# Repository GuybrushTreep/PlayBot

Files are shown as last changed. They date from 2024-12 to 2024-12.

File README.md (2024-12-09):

# 🤖 PlayBot

PlayBot is an unofficial, experimental accessory for Panic Inc.'s Playdate handheld console, which transforms your console into a lovely little desktop robot. 
With its integrated charging capabilities, it can serve as a charging dock for your Playdate.

Here is a little video of Playbot (click to watch)

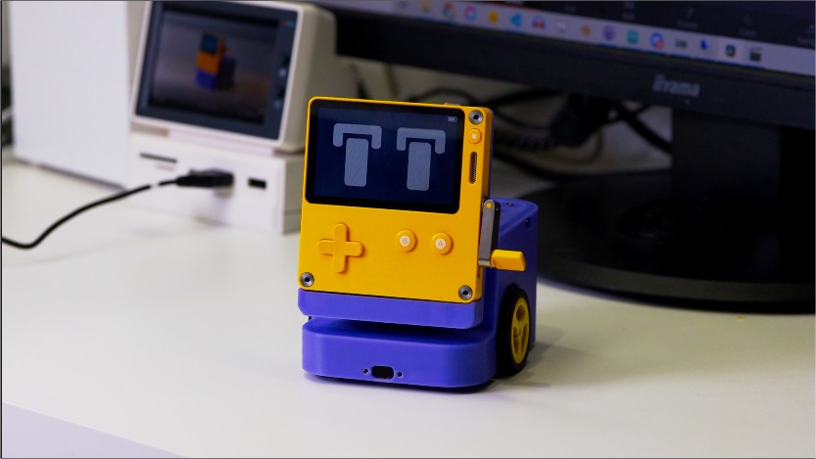
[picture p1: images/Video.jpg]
Playbot_Trailer (https://youtu.be/pZ3aDawW1vo?si=pN9pur77LKVZNdHx)


⚡ Battery life: ~45 min of autonomous operation per charge.

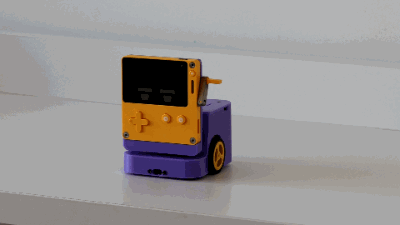
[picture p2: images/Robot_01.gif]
PlaybotAction
 PlaybotAction
PlaybotAction PlaybotAction

## ⚠️ Disclaimer

This project is not affiliated with nor endorsed by [Panic](https://panic.com/).

I cannot be held responsible for any damage, data loss, short circuit, burned down house, etc. 😘

## 🔧 Hardware

The project is based on a Teensy 4.1 microcontroller that acts as a USB hub for the Playdate and communicates over serial. 

The Playdate acts as the robot's brain and sends commands to the Teensy to control motors and gather various sensor values:

- 2 TOF distance sensors
- TEMT6000 Ambient light sensor
- 2 IR sensors
- Dual motors with encoders
- MAX1704X fuel gauge 

I'm also using the Playdate's integrated sensors:
- Accelerometer
- Microphone

Additionnal Vision AI camera powered by [Huskylens](https://www.dfrobot.com/product-1922.html) will be compatible.

PlayBot's frame is fully 3D printed. A complete bill of materials and assembly instructions can be found [here](https://github.com/GuybrushTreep/PlayBot/tree/main/hardware) 

## 💾 Firmware

You can flash the [firmware](https://github.com/GuybrushTreep/PlayBot/tree/main/src/PlayBot) using the Arduino IDE and Teensyduino add-on available [here](https://www.pjrc.com/teensy/teensyduino.html).

## 📚 Dependencies 
  - [USBHost_t36](https://github.com/PaulStoffregen/USBHost_t36) by [PaulStoffregen](https://github.com/PaulStoffregen)
  - [Encoder](https://github.com/PaulStoffregen/Encoder) by [PaulStoffregen](https://github.com/PaulStoffregen) 
  - [drv8835-motor-shield](https://github.com/pololu/drv8835-motor-shield) by [pololu](https://github.com/pololu)
  - [SD library](https://github.com/arduino-libraries/SD) by [Arduino](https://github.com/arduino-libraries)
  - [Servo library](https://github.com/arduino-libraries/Servo) by [Arduino](https://github.com/)
  - [MAX1704X](https://github.com/adafruit/Adafruit_MAX1704X) by [adafruit](https://github.com/adafruit)
  - [PID_V1](https://github.com/br3ttb/Arduino-PID-Library) by [br3ttb](https://github.com/br3ttb)
  - [WS2812FX](https://github.com/kitesurfer1404/WS2812FX) by [kitesurfer1404](https://github.com/kitesurfer1404/WS2812FX)
  - [CircularBuffer](https://github.com/rlogiacco/CircularBuffer) by [rlogiacco](https://github.com/kitesurfer1404/WS2812FX)

## 📱 Companion App

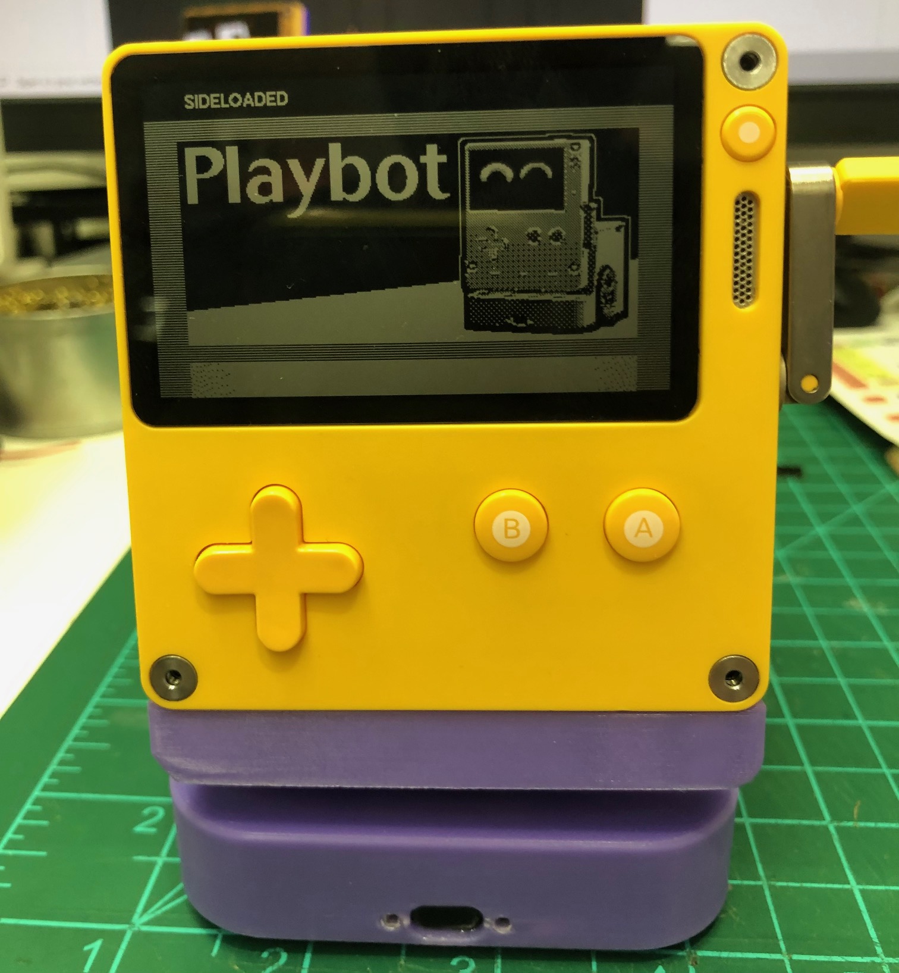
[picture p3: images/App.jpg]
Power Board


The app, written in Lua, needs to be sideloaded onto the Playdate and is located in a [separate repository](https://github.com/GuybrushTreep/pd-playbot-app).

## 🎨 Custom rig
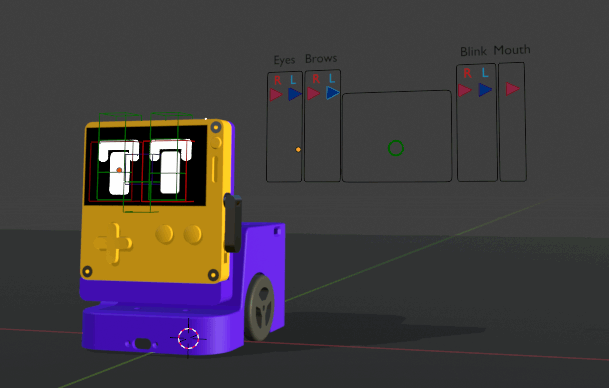
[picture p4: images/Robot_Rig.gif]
PlaybotRig


A Custom rig and sequence exporter written in python is also available for Blender in a [seperate repository](https://github.com/GuybrushTreep/Playbot_Rig).
Animate, render and export custom animation sequences!

## ⚠️ Known Issues
* ToF sensors show unreliable readings when pointing into empty space (possibly defective units) - planning to replace with IR sensors
* Battery gauge readings become erratic under high current load - investigation ongoing

## 📜 License

[MIT](https://choosealicense.com/licenses/mit/)

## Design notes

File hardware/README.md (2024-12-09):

## Summary
- [Bill of materials](#bill-of-materials)
- [Recommended tools](#Recommended-tools)
- [3d printed parts](#3d-printed-parts)
- [Custom PCBs](#custom-pcbs)
    - [Power board](#power-board)
    - [Main board](#main-board)
- [Assembly](#assembly)
    - [Top Frame](#Top-Frame)
        - [Servo mod](#servo-modification)
        - [Brass insert](#brass-inserts)
    - [Middle Frame](#middle-frame)
        - [DRV8835](#drv8835)
        - [Power harness](#power-harness)
    - [Lower Frame](#lower-frame)
        - [Ball caster wheels](#ball-caster-wheels)
        - [ITR20001-sensors](#itr20001-sensors)
    - [console base](#console-base)
        - [Usb](#usb)  
    - [Shell](#Shell)
        - [light sensor](#TEMT6000-light-sensor)
        - [switch](#SPDT-switch)
        - [TOF10120](#TOF-sensors)
     - [Putting Everything Together](#Putting-Everything-Together)
# Bill of materials

This folder contains all the files and instructions to build Playbot.

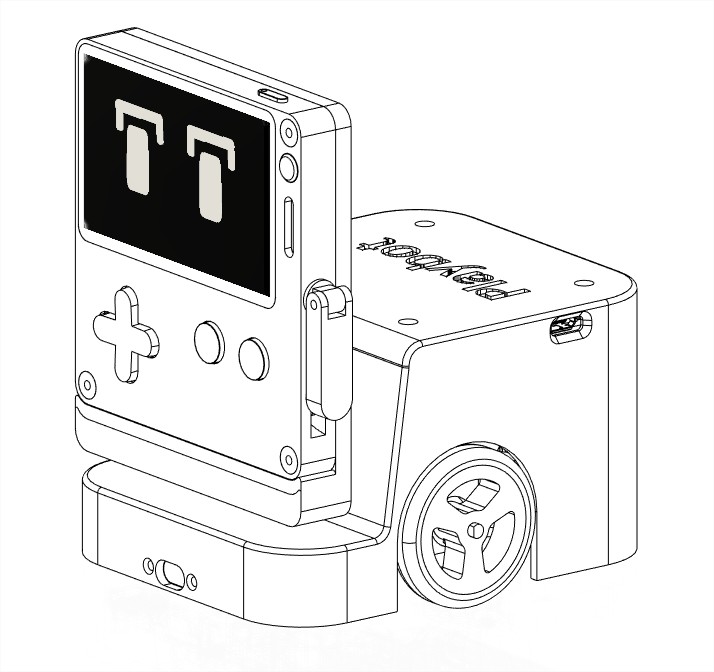
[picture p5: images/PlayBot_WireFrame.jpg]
A drawing of the robot from Fusion


## Hardware

|Item| Quantity|Notes
|---|---|---|
|Custom PCBs|2|Order from [JLCPCB](https://jlcpcb.com) see Gerber files and BOMs
|Teensy 4.1 microcontroller| 1|[PJCRC store](https://www.pjrc.com/store/teensy41.html)
| TOF10120| 2| [AlliExpress](https://fr.aliexpress.com/item/1005006355757514.html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,scm-url:1007.40050.354490.0,pvid:43a39a83-8bf7-4a9d-b2aa-4d4200da0014,tpp_buckets:668%232846%238107%231934&isseo=y&pdp_npi=4%40dis%21EUR%214.29%214.29%21%21%214.68%214.68%21%402103895417271255595797778e7ce3%2112000037973716121%21rec%21FR%21%21ABXZ&utparam-url=scene%3ApcDetailTopMoreOtherSeller%7Cquery_from%3A)
| Low profile headers 12 pins| 1| [Example  AlliExpress](https://fr.aliexpress.com/item/1005006252502654.html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)
| SG90 servo | 1 | [Example AlliExpress](https://fr.aliexpress.com/item/1005006522732429.html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)
| ITR20001 | 2| [Example AlliExpress](https://fr.aliexpress.com/item/1005007697148589.html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)
TEMT6000 ambient light sensor | 1 | [Example AlliExpress](https://fr.aliexpress.com/item/33034437035.html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)
| mini ball caster wheels| 2| [Example AlliExpress](https://fr.aliexpress.com/item/1005007392098564.html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,scm-url:1007.40050.354490.0,pvid:af027fb5-cab6-4c62-8038-6874711e65c5,tpp_buckets:668%232846%238112%231997&isseo=y&pdp_npi=4%40dis%21EUR%210.21%210.21%21%21%210.23%210.23%21%402103895417271259822313224e7ce3%2112000040559594027%21rec%21FR%21%21ABXZ&utparam-url=scene%3ApcDetailTopMoreOtherSeller%7Cquery_from%3A)
| N20 6V 500RPM motors| 2| [Example AlliExpress](https://fr.aliexpress.com/item/1005004999529855.html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)
| N20 wheels| 2| [Example AlliExpress](https://fr.aliexpress.com/item/1005006640418754.html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)
| DRV8835 Dual Motor Driver Carrier| 1| [Pololu](https://www.pololu.com/product/2135)
| M2 Screws| 1 box| [Example AlliExpress](https://fr.aliexpress.com/item/1005002426046826.html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)
| M2 and M3 nylon nut set| | [Example Alliexpress](https://fr.aliexpress.com/item/33017191364.html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)
| M2 X 5 insert| 1 box| [Example AlliExpress](https://fr.aliexpress.com/item/1005007481465353.html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)
| USBC connectors Male/Female| 1 | [Example AlliExpress](https://fr.aliexpress.com/item/1005004807492800.html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)
| SPDT switch| 1 | [Example AlliExpress](https://fr.aliexpress.com/item/32812689209.html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)
| Battery Lipo 1S 15000mAh 504050 | 1 | [Example AlliExpress](https://fr.aliexpress.com/item/32988366494.html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)
| Pre crimped JST SH connector set 3 to 7 pins (pre crimped is much easier)| 1 | [Example AlliExpress](https://fr.aliexpress.com/item/1005004705798387.html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)
| JST PH connector Male/Female 2/4 pins | 1 box | [Example AlliExpress](https://fr.aliexpress.com/item/1005006498660940.html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)
| Flanged ball bearing 6X3X2.5 | 2 | [Example AlliExpress](https://fr.aliexpress.com/item/32969015516.html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)
| Nylon M3 X 40 screw  | 1 | [Example AlliExpress](https://fr.aliexpress.com/item/1005003130662735.html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)
| Magnets 6X3| 4 | [Example AlliExpress](https://fr.aliexpress.com/item/1005006291065081.html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)
| Servo pull rod 120 mm| 1 | [Example AlliExpress](https://www.aliexpress.us/item/3256807116664206.html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)
| 1.3mm push rod connector| 1 |[Example AlliExpress](https://www.aliexpress.us/item/2255800230609318.html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)
| Micro SD card| 1 |
| 24 AWG wire in various colors| 1 |
| HuskyLens (optional, for advanced AI vision) | 1 | [DFRobot](https://www.dfrobot.com/product-1922.html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)
|A playdate !| 1 | [Play.date](https://play.date/)

**Price range**: Around 100/120 $ (without shipping) **per bot**. Custom PCBs are cheap (10$ a piece) but you have to order in bulk of 5. 

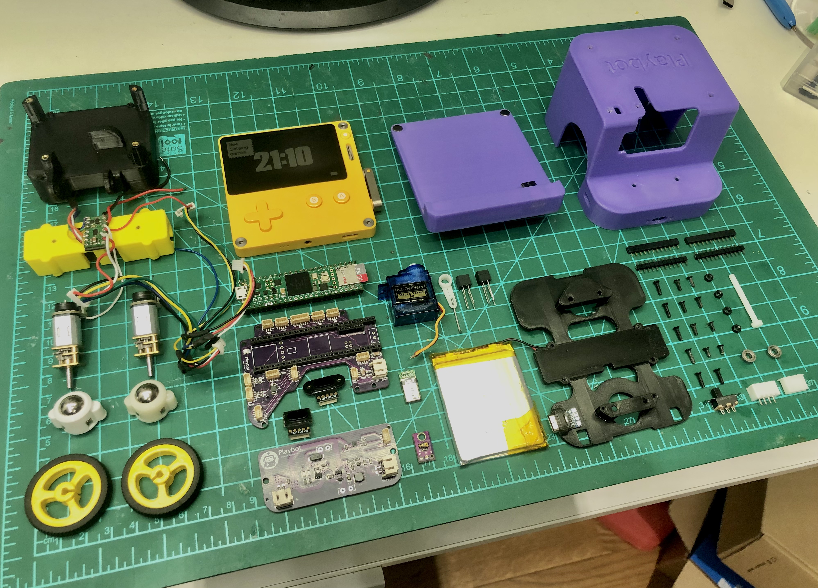
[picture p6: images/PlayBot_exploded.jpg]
Parts


⚠️⚠️ Playbot is not a plug-and-play project as it requires a lot of soldering and custom connectors/wires. ⚠️⚠️

**This is a first prototype, and I'm already working on a V2 with only one PCB and less soldering involved.**

## Recommended tools

| Tool | Notes |
|---|---|
| Soldering Iron |  |
| Flux | For clean solder joints |
| Heat Shrink Tubing | 1/2 mm|
| Precision Screwdrivers |  |
| JST PH Crimp Tool | For JST PH connectors |
| JST SH Crimp Tool | Optional - expensive, can use pre-crimped wires instead |
| Kapton Tape |  |
|  Wire strippers  | (20-30 AWG) |
|  Tweezers  ||
|  Helping hands with magnifying glass|  |

## 3D Printed Parts

STL files are available [here](../hardware/3dPrinted_Parts)

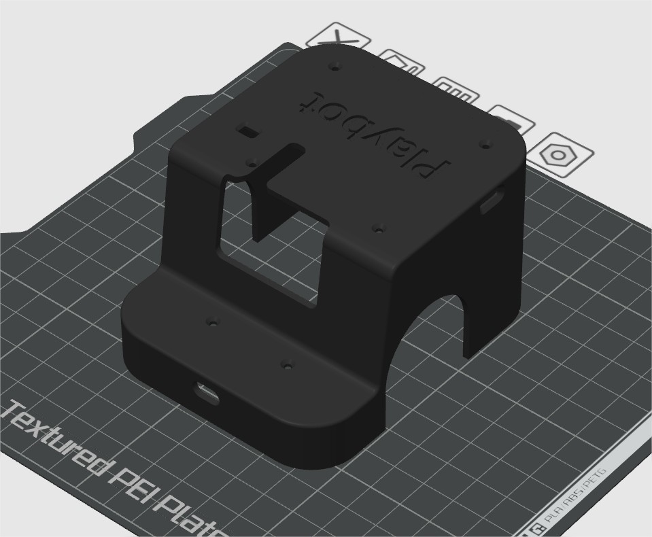
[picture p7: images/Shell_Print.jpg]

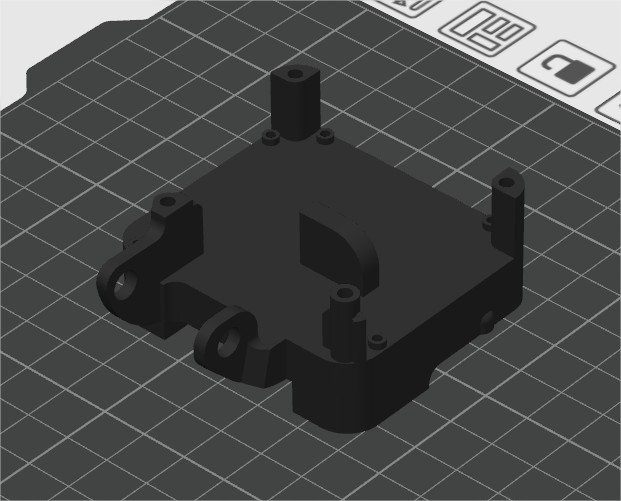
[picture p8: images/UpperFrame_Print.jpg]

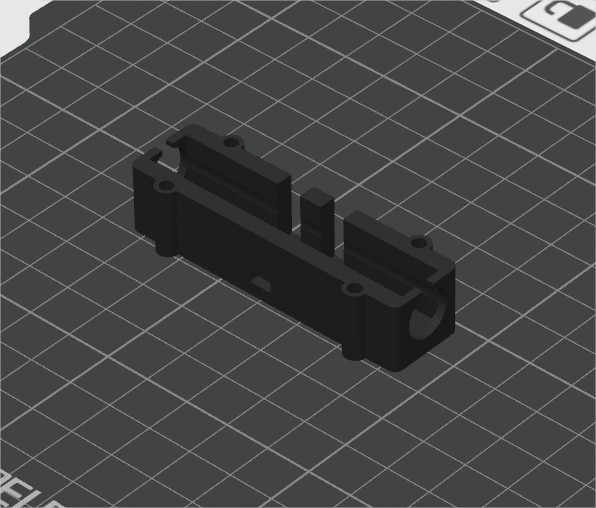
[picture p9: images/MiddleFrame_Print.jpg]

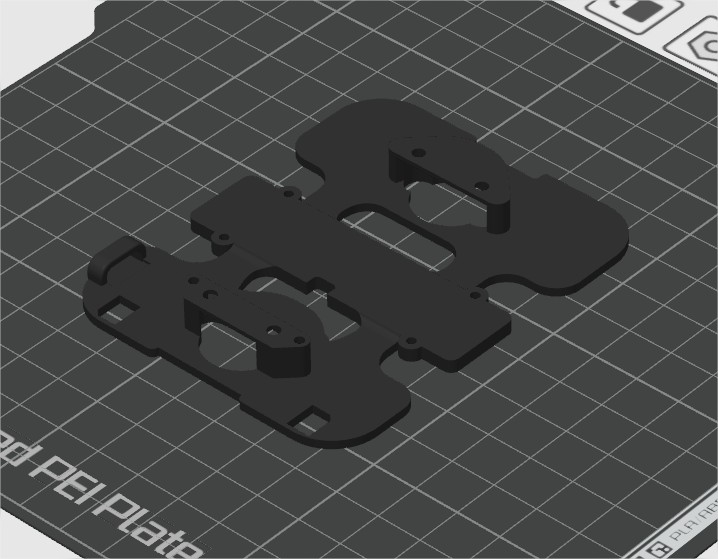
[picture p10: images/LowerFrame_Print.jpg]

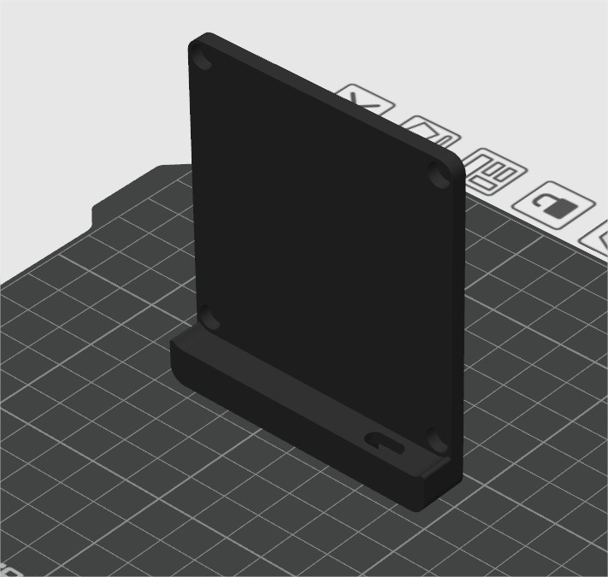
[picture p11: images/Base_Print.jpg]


I print these on a Bambu Lab A1 mini with generic PLA. 

## Custom PCBs
### Power Board
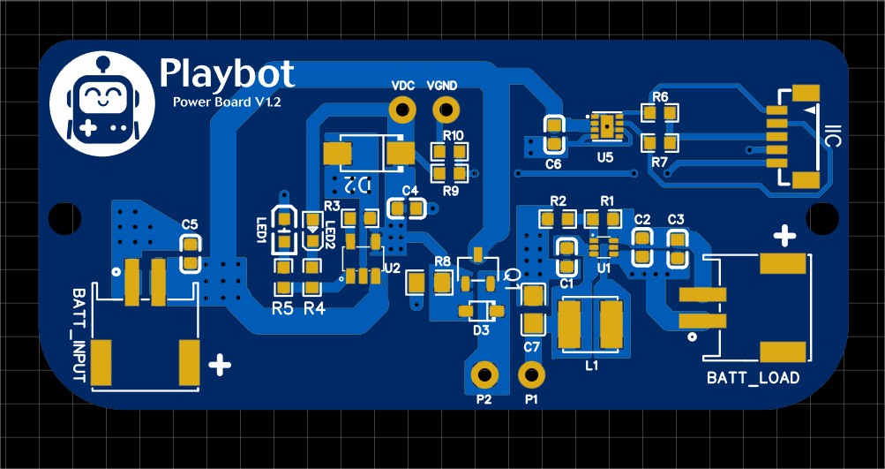
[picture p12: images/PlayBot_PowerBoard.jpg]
Power Board

1-cell LiPo charger (MCP73831) with 5V boost converter (TPS61023) and fuel gauge (MAX17048). The board is capable of load-sharing and can be plugged in while running the robot. 
This board will also charge the Playdate when the robot is active. 
Red LED when charging/Yellow LED when fully charged.

### Main Board 

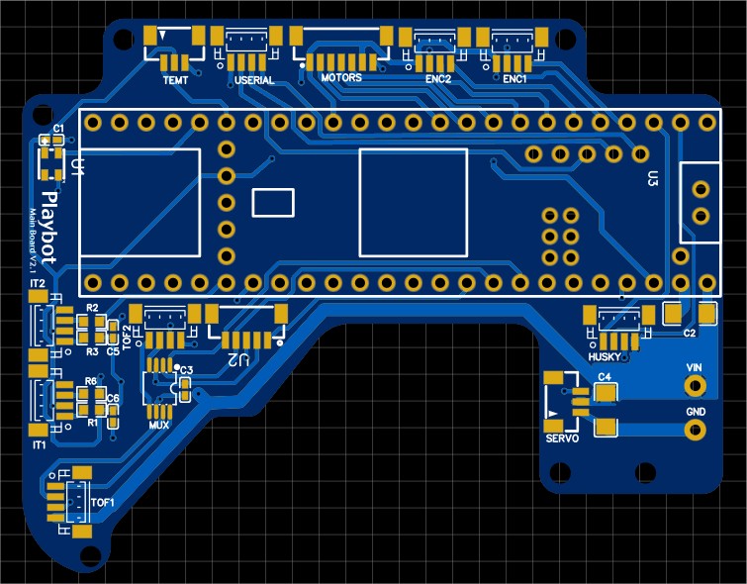
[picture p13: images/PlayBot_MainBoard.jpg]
Main board


A board that connects various sensors/motors/servos and distributes power to the Teensy.
You will need special low-profile headers to fit the Teensy inside the case.
 
 ⚠️⚠️ **Important: To protect your battery-powered Teensy, it is recommended to cut the USB power trace.** ⚠️⚠️

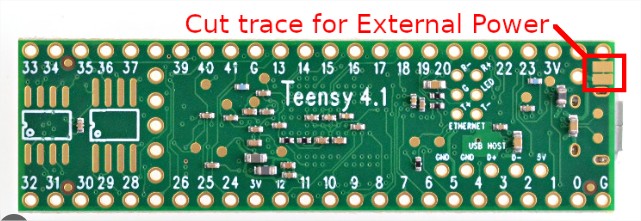
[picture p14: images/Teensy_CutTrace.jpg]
 

- Solder male headers on Teensy main side pins and USB host pins.

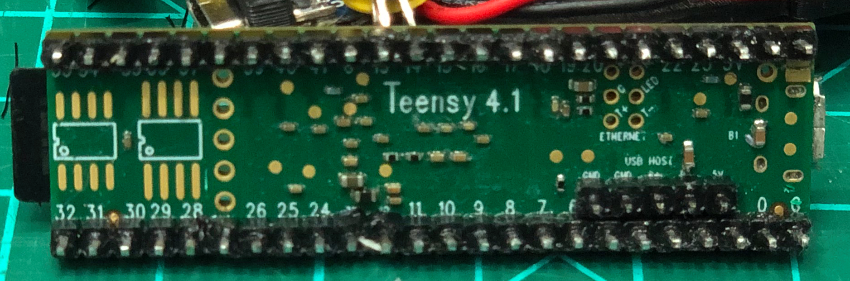
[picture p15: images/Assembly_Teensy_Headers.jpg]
 

- Solder female low-profile headers on the Playbot main board. 

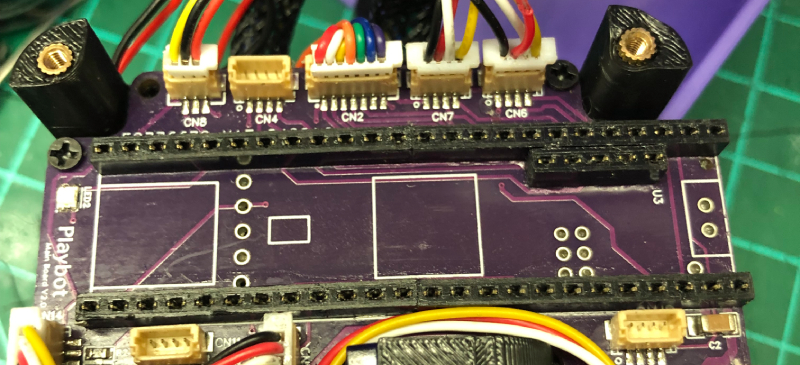
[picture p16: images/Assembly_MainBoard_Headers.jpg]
Main board
 

## Assembly

### Testing

⚠️⚠️ For every step, I strongly advise you to double-check your connections, flash the test [firmware](https://github.com/GuybrushTreep/PlayBot/tree/main/src/Playbot_SensorsTest) to the Teensy, plug in your components, and test the boot sequence to ensure everything is working correctly. ⚠️⚠️ 

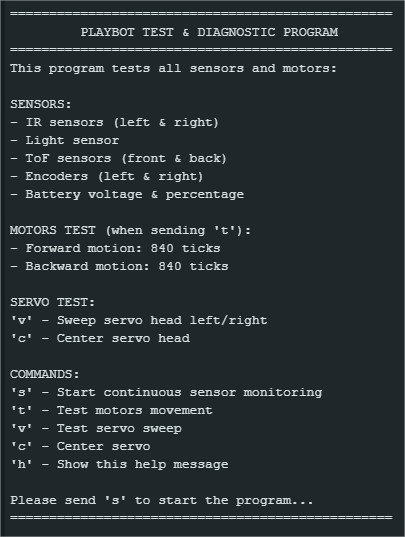
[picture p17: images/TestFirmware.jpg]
Test


### Top Frame

Main board

#### Servo Modification:

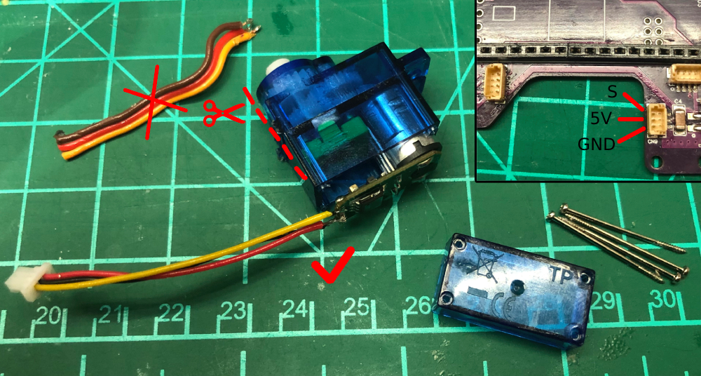
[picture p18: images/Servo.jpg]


- Cut the left plastic ear flush.
- Open the servo case by removing the 4 screws.
- Cut/desolder the wires. Take note of the color code: **brown** -> **GND** | **red** -> **V+** | **orange** -> **signal**.
- Solder new wires with a JST SH connector. Pay attention to the **servo** connector wiring. 

Also, due to tight space constraints, the servo horn needs to be modified.

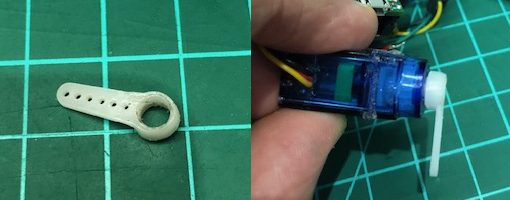
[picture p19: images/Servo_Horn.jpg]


The hole is enlarged with a soldering iron and press-fitted onto the servo axle while soft, center the servo position with the test firmware before screwing it.

#### Brass Inserts

Check this excellent [tutorial](https://www.youtube.com/watch?v=KC1LLU54DKU&ab_channel=GeekDetour) for heated brass inserts on PLA.

- Add 5 brass inserts on the top of the frame:

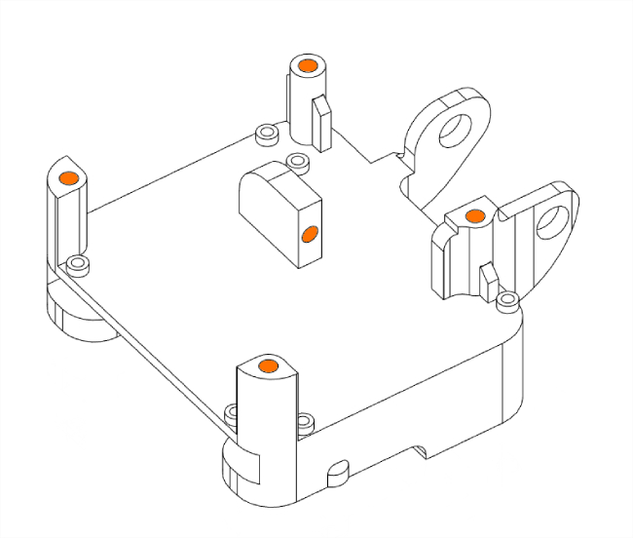
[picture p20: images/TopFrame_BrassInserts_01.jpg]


- And 4 others on the frame's bottom: 

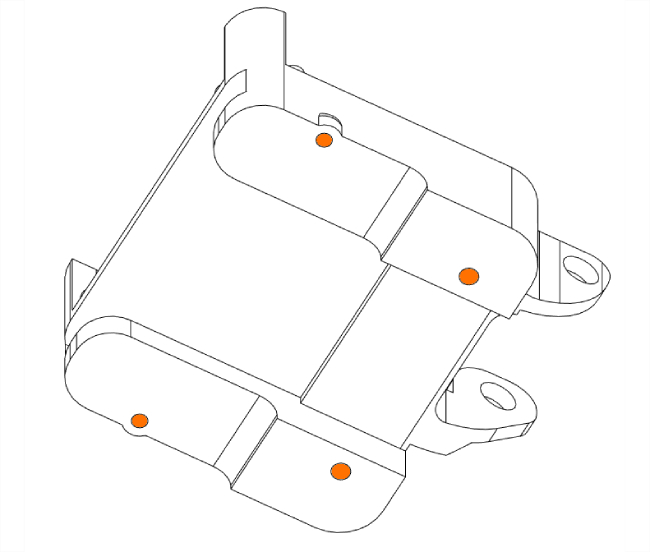
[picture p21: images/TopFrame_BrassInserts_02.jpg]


- Screw the mainboard directly into the frame using M2 * 4 screws.
- Press-fit the 2 ball bearings into the frame
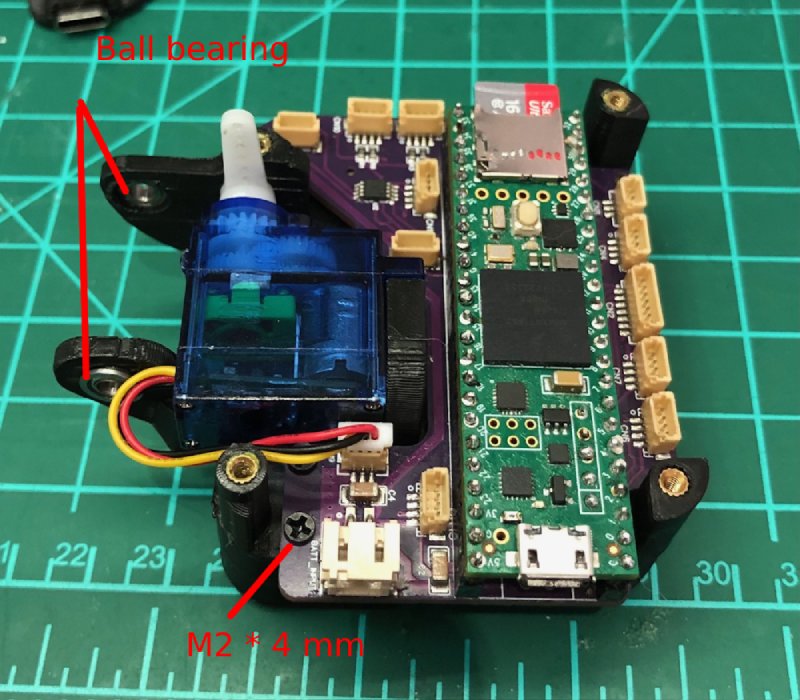
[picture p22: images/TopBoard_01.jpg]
Main board


- Solder the power switch and USB-C input to the power management board. Press-fit the USB-C plug into the bottom frame. You can add a bit of hot glue to secure it to the frame.
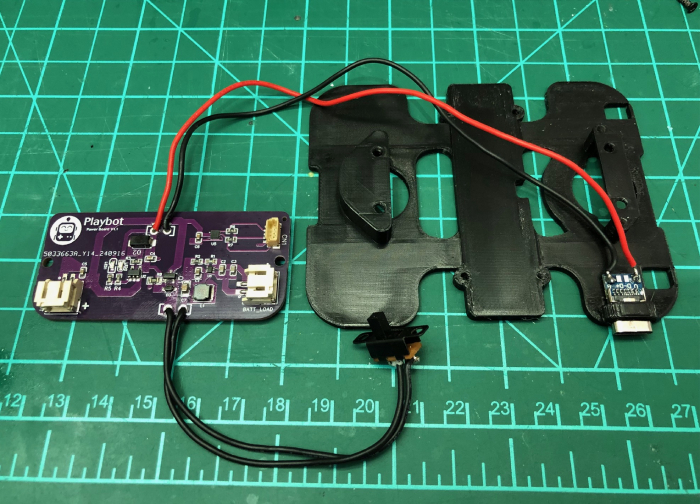
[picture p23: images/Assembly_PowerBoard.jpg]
Main board


- You can now screw the power board to the frame's bottom. 
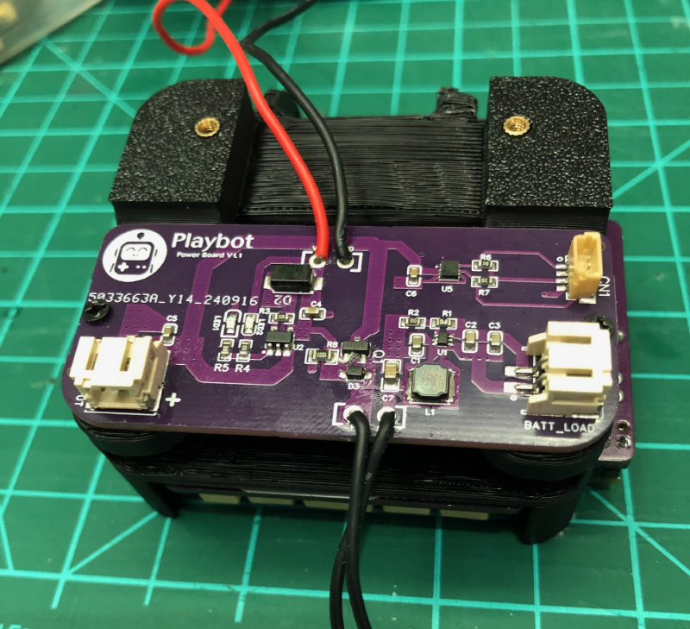
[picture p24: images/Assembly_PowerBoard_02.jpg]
Main board


- The lipo baterry slides into a dedicated socket on the frame.
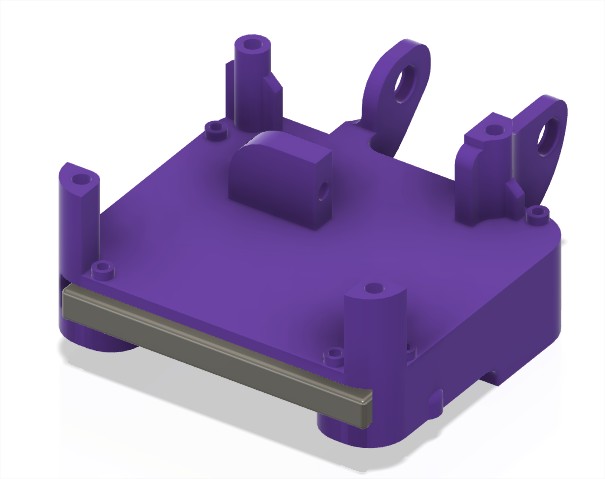
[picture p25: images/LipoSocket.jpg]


### Middle Frame
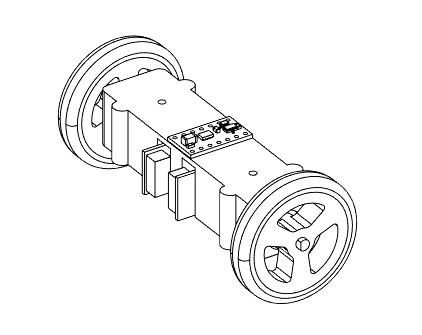
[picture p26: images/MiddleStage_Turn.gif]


- Add 4 brass inserts.

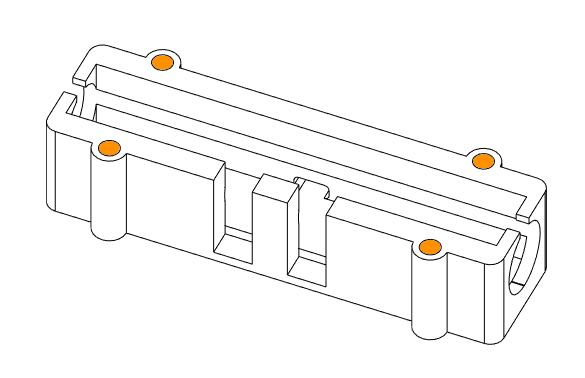
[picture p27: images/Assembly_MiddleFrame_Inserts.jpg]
Middle_01


#### DRV8835
The DRV8835 board is attached directly in the middle of the part with double-sided adhesive.

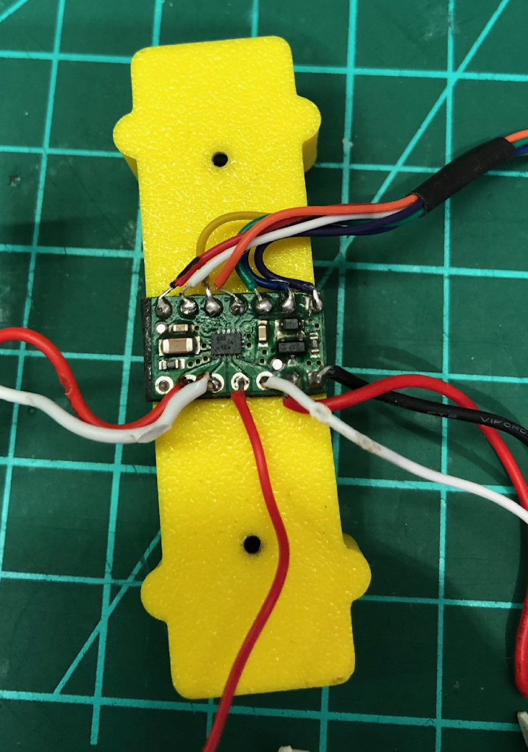
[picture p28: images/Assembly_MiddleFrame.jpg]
Middle_01


- Solder pins MODE, AIN1, AIN2, BIN1, BIN2, VCC, and GND to a 7-pin JST SH connector for the motors Connector.

Please check the [Pololu](https://www.pololu.com/product/2135) page for more information about this board.

DRV8835

- Create a custom plug for motors. Power comes from the DRV8835 board (M1 and M2), and the 4 other wires are for encoder feedback (ENC1, ENC2).

Motors
Motors

- Before adding motors, you must attach the middle and top frame together with 2 M2 screws. 

MiddleFrame

#### Power Harness

Create a power harness with JST **PH** connectors to power the main board and DRV8835 from the power board's power output. 

PowerHarness

** note: I replaced the Main board's PH connector with simple solder pads on the last revision** 

## Lower Frame
LowerStage

### Ball Caster Wheels

- Remove screws, insert the ball caster wheels, and screw them back to the frame.
BallCaster

## Console Base 

ConsoleBase

### USB 

- Create a USB plug connected to a 4-pin JST **PH** connector. 
You can add a bit of hot glue to secure the PH connector.

Base_USB

- Create a 4-pin **PH** to **SH** connector that will connect to **USERIAL** connector on the main board.

Base_Plug

Base_Plug

The USB plugs comes with little plastic rings that you can glue to the part.

- Press-fit magnets into the dock.

Magnet

## Shell
Shell

### TEMT6000 Light Sensor

- Solder a 3-pin JST **SH** connector that connects to **TEMT** connector on the main board.

TEMT

- Screw and bolt it to the shell.

TEMT02

### SPDT Switch

- Screw and bolt the switch to the shell.

Switch

### TOF Sensors

- Solder a 4-pin JST **SH** connector that connects to **TOF1** and **TOF2** on the main board. You can cut RX/TX wires as we use I²C through a 2-channel multiplexer.

TOF01

- Attach both sensors at the front and back of the shell with M2.5x6 screws and nylon nuts. 

TOF01

## Putting Everything Together

At this point, you're almost done. Congratulations! I assume you've already tested every component by flashing the test firmware. 

⚠️⚠️ Don't forget to flash the micro SD card with the [animation files](https://github.com/GuybrushTreep/Playbot_Rig/tree/main/Animations/Export). You can still access the SD card from your computer with the help of this library: https://github.com/KurtE/MTP_Teensy ⚠️⚠️

If no errors show up, you're good to assemble the remaining parts in this order:

TOF01
TOF01
TOF01
TOF01
TOF01

This is the tricky part, as everything will be tightly packed inside the shell.

Attach the screen base with M3 screw, do not overtighten it. 
Cut a Servo pull rod at 20 mm and attach it to the servo's arm with a connector.

TOF01

Congratulations, your Playbot is now complete!

TOF01

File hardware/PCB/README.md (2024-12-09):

# JLCPCB Options

Parts

Parts

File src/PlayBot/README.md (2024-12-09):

# Robot Controller - Arduino Project

Firmware for a robot using Teensy microcontroller that communicates with a Playdate device.

## Core Components

### Main Program (PlayBot.ino)
- Main program loop and initialization
- Orchestrates all subsystems
- Manages communication between components

### Managers

#### AnimationManager (AnimationManager.h)
- Handles animation playback from SD card
- Controls servo movements
- Manages motor coordination for animations
- Real-time frame processing

#### BatteryManager (BatteryManager.h)
- Battery voltage monitoring via MAX17048 gauge
- Charging state detection
- Power state reporting to Playdate

#### CommunicationManager (CommunicationManager.h)
- USB serial communication with Playdate
- Message parsing and routing
- Protocol handling for all subsystems

#### LEDController (LEDController.h)
- WS2812 LED control
- Status indication

#### MotorController (MotorController.h)
- DRV8835 motor driver control
- PID-based motor control
- Encoder feedback processing
- Rotation and movement commands

#### SensorManager (SensorManager.h)
- ToF distance sensors management
- IR edge detection
- Light sensor readings
- Collision detection
- Sensor data aggregation and reporting

#### StorageManager (StorageManager.h)
- SD card initialization
- File system management

### Support Files

#### Config.h
- System-wide configuration parameters
- Pin definitions
- Timing constants
- Sensor thresholds

#### Debug.h/cpp
- Debugging infrastructure
- Error logging
- Setup error tracking
- Log buffering and transmission

#### DistanceTracker.h
- Tracks total distance traveled
- Persistent distance logging
- Movement statistics

#### HardwareConfig.h/cpp
- Hardware-specific configurations
- Pin assignments
- Physical constants
- Hardware object initialization

## Communication Protocol

Message Protocol Details:

Outgoing (Arduino -> Playdate):
- "msg b/percent/voltage/charging"
  Example: "msg b/85.20/3.7/1" (85.20% battery, 3.7V, charging)

- "msg d/irRight/irLeft/tofFront/tofBack/encRight/encLeft/light/batteryVoltage/charging/distanceM"
  Example: "msg d/100/120/150.20/160.50/-1200/1200/500/3.7/1/1.50"
  (IR values, ToF in mm, encoder ticks, light level, battery V, charging state, distance in meters)

- "msg e/1" (Edge detected)

- "msg l/0" or "msg l/1" (Darkness state change: 0=dark, 1=light)

- "msg p/0" or "msg p/1" (Power/charging state: 0=unplugged, 1=charging)

- "msg s/" (Connection confirmation)

- "msg w/1" (Collision detected)

- "msg r/1" (Rotation completed)

Incoming (Playdate -> Arduino):
- "a/filepath" (Start animation from SD card)

- "b" (Request battery status)

- "d" (Request sensor data)

- "v" (Connection verification ping)

- "t/turns/direction"
  Example: "t/2/1" (2 turns, direction 1=clockwise, -1=counterclockwise)

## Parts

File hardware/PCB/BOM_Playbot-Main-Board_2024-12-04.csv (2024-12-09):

ID | Name | Designator | Footprint | Quantity | Manufacturer Part | Manufacturer | Supplier | Supplier Part | Price | JLCPCB Part Class
1 | WS2812C-2427 | U1 | LED-SMD_4P-L2.7-W2.4-TL_WS2812C-2427 | 1 | WS2812C-2427 | worldsemi | LCSC | C4154872 | 0.092 | Extended Part
2 | BM05B-SRSS-TB(LF)(SN) | BATTDATA | CONN-SMD-5P-P1.00_BM05B-SRSS-TB-LF-SN | 1 | BM05B-SRSS-TB(LF)(SN) | JST | LCSC | C160391 | 0.257 | Extended Part
3 | BM04B-SRSS-TB(LF)(SN) | ENC1,ENC2,HUSKY,IT1,IT2,TOF1,USERIAL | CONN-SMD_BM04B-SRSS-TB | 7 | BM04B-SRSS-TB(LF)(SN) | JST | LCSC | C160390 | 0.167 | Extended Part
4 | BM07B-SRSS-TB(LF)(SN) | MOTORS | CONN-SMD_7P-P1.00_BM07B-SRSS-TB | 1 | BM07B-SRSS-TB(LF)(SN) | JST | LCSC | C160393 | 0.232 | Extended Part
5 | PCA9540BDP,118 | MUX | TSSOP-8_L3.0-W3.0-P0.65-LS4.9-BL | 1 | PCA9540BDP,118 | NXP(恩智浦) | LCSC | C2652901 | 1.514 | Extended Part
6 | BM03B-SRSS-TBT(LF)(SN) | SERVO,TEMT | CONN-SMD_BM03B-SRSS-TBT-LF-SN | 2 | BM03B-SRSS-TBT(LF)(SN) | JST | LCSC | C495538 | 0.289 | Extended Part
7 | BM04B-SRSS-TB(LF)(SN) | TOF2 | CONN-SMD_BM04B-SRSS-TB | 1 | BM04B-SRSS-TB(LF)(SN) | JST | LCSC | BM04B-SRSS-TB |  | Extended Part
8 | 100nF | C1,C3,C5,C6 | C0402 | 4 | CL05B104KO5NNNC | SAMSUNG(三星) | LCSC | C1525 | 0.001 | Basic Part
9 | 1MMHOLE_PTH | GND,VIN | 1MMHOLE_PTH | 2
10 | TEENSY4.1 COMPLETE | U3 | TEENSY4.1 - KB | 1 | Teensy4.1 | PJRC
11 | 100uF | C2,C4 | C1206 | 2 | CL31A107MQHNNNE | SAMSUNG(三星) | LCSC | C15008 | 0.061 | Basic Part
12 | 220Ω | R1,R3 | R0603 | 2 | 0603WAF2200T5E | UNI-ROYAL(厚声) | LCSC | C22962 | 0.001 | Basic Part
13 | 10kΩ | R6,R2 | R0603 | 2 | 0603WAF1002T5E | UNI-ROYAL(厚声) | LCSC | C25804 | 0.001 | Basic Part

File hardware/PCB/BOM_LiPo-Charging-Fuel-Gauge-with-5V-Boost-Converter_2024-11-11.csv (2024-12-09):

ID | Name | Designator | Footprint | Quantity | Manufacturer Part | Manufacturer | Supplier | Supplier Part | Price | Pins | Contributor | JLCPCB Part Class
1 | PH-2AWB | BATT_INPUT,BATT_LOAD | CONN-SMD_PH-2AWB | 2 | PH-2AWB | DLL(德利) | LCSC | C20598817 | 0.096 | 4 | lcsc | Extended Part
2 | 10uF | C1 | C0603 | 1 | CL10A106KP8NNNC | SAMSUNG(三星) | LCSC | C19702 | 0.005 | 2 |  | Basic Part
3 | 22uF | C2,C3 | C0603 | 2 | CL10A226MQ8NRNC | SAMSUNG(三星) | LCSC | C59461 | 0.008 | 2 |  | Basic Part
4 | 4.7uF | C4,C5 | C0603 | 2 | CL10A475KO8NNNC | SAMSUNG(三星) | LCSC | C19666 | 0.009 | 2 |  | Basic Part
5 | 100nF | C6 | C0603 | 1 | CC0603KRX7R9BB104 | YAGEO(国巨) | LCSC | C14663 | 0.002 | 2 |  | Basic Part
6 | 1uF | C7 | C0805 | 1 | CL21B105KBFNNNE | SAMSUNG | LCSC | C28323 | 0.008 | 2 |  | Basic Part
7 | SMAJ5.0A_C2925443 | D2 | SMA_L4.3-W2.6-LS5.0-RD | 1 | SMAJ5.0A | Liown(里阳半导体) | LCSC | C2925443 | 0.029 | 2 | lcsc | Extended Part
8 | NSR0320MW2T1G | D3 | SOD-323_L1.8-W1.3-LS2.5-RD | 1 | NSR0320MW2T1G | onsemi(安森美) | LCSC | C48192 | 0.052 | 2 |  | Extended Part
9 | 1uH | L1 | IND-SMD_L4.0-W4.0 | 1 | XRNR4018-1.0uH/N | XR(祥如) | LCSC | C5289338 | 0.034 | 2 | lcsc | Extended Part
10 | XL-1608SURC-06 | LED1 | LED0603-RD_RED | 1 | XL-1608SURC-06 | XINGLIGHT(成兴光) | LCSC | C965799 | 0.003 | 2 | LCSC
11 | SZYY0603YG | LED2 | LED0603-R-RD_GREEN | 1 | SZYY0603YG | yongyu(永裕光电) | LCSC | C434423 | 0.011 | 2 | LCSC | Extended Part
12 | 1MMHOLE_PTH | P1,P2,VDC,VGND | 1MMHOLE_PTH | 4 |  |  |  |  |  | 1 | Components
13 | SI2301CDS-T1-GE3 | Q1 | SOT-23-3_L3.0-W1.7-P0.95-LS2.9-BR | 1 | SI2301CDS-T1-GE3 | VISHAY(威世) | LCSC | C10487 | 0.058 | 3 |  | Basic Part
14 | 732kΩ | R1 | R0603 | 1 | RC0603FR-07732KL | YAGEO(国巨) | LCSC | C246003 | 0.001 | 2 | LCSC | Extended Part
15 | 100kΩ | R2 | R0603 | 1 | 0603WAF1003T5E | UNI-ROYAL(厚声) | LCSC | C25803 | 0.001 | 2 |  | Basic Part
16 | 2kΩ | R3,R10 | R0603 | 2 | 0603WAF2001T5E | UNI-ROYAL(厚声) | LCSC | C22975 | 0.001 | 2 |  | Basic Part
17 | 1kΩ | R4,R5,R9 | R0603 | 3 | 0603WAF1001T5E | UNI-ROYAL(厚声) | LCSC | C21190 | 0.001 | 2 |  | Basic Part
18 | 10kΩ | R6,R7 | R0603 | 2 | 0603WAF1002T5E | UNI-ROYAL(厚声) | LCSC | C25804 | 0.001 | 2 |  | Basic Part
19 | 100k | R8 | R0805 | 1 | 0805W8F1003T5E | Uniroyal Elec | LCSC | C149504 | 0.002 | 2 | LCSC | Extended Part
20 | BM05B-SRSS-TBT(LF)(SN) | TEST | CONN-SMD_BM05B-SRSS-TBT-LF-SN | 1 | BM05B-SRSS-TBT(LF)(SN) | JST | LCSC | C265092 | 0.339 | 7 | LCSC | Extended Part
21 | TPS61023DRLR | U1 | SOT-563_L1.6-W1.2-P0.50-LS1.6-BR | 1 | TPS61023DRLR | TI(德州仪器) | LCSC | C919459 | 0.24 | 6 | LCSC | Extended Part
22 | MCP73831T-2ATI/OT | U2 | SOT-23-5_L3.0-W1.7-P0.95-LS2.8-BR | 1 | MCP73831T-2ATI/OT | MICROCHIP(美国微芯) | LCSC | C14879 | 0.998 | 5 |  | Extended Part
23 | MAX17048G+T10 | U5 | DFN-8_L2.0-W2.0-P0.50-BL-EP | 1 | MAX17048G+T10 | ADI(亚德诺)/MAXIM(美信) | LCSC | C2682616 | 0.995 | 9 | LCSC | Extended Part

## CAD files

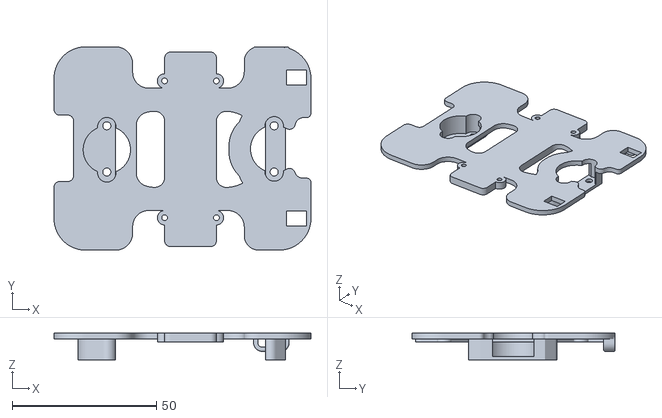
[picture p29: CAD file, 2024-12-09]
hardware/3dPrinted_Parts/PlayBot_LowerFrame.stl
89.1 x 70.5 x 9.20

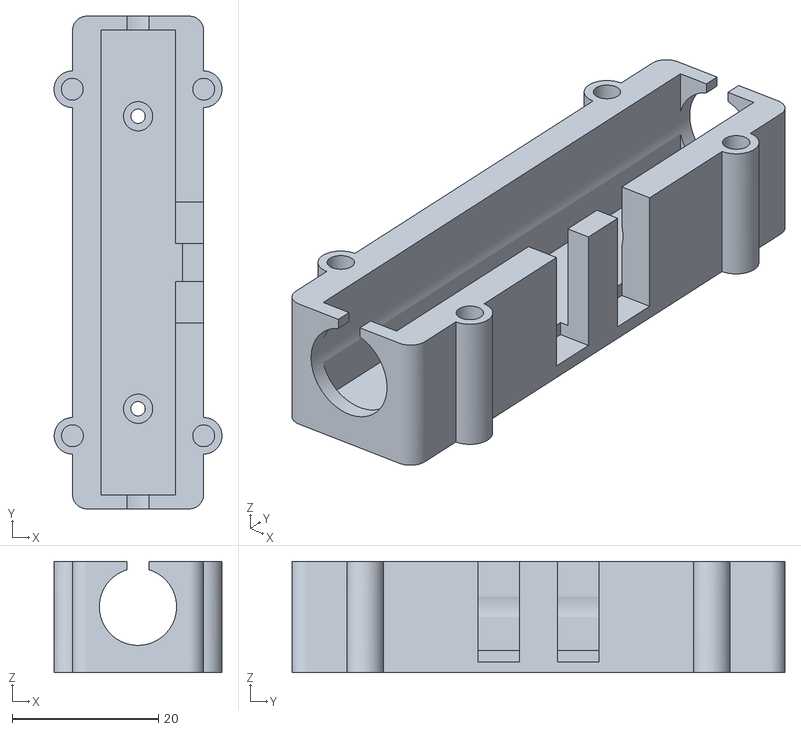
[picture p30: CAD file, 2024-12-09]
hardware/3dPrinted_Parts/PlayBot_MiddleFrame.stl
23.0 x 67.4 x 15.2

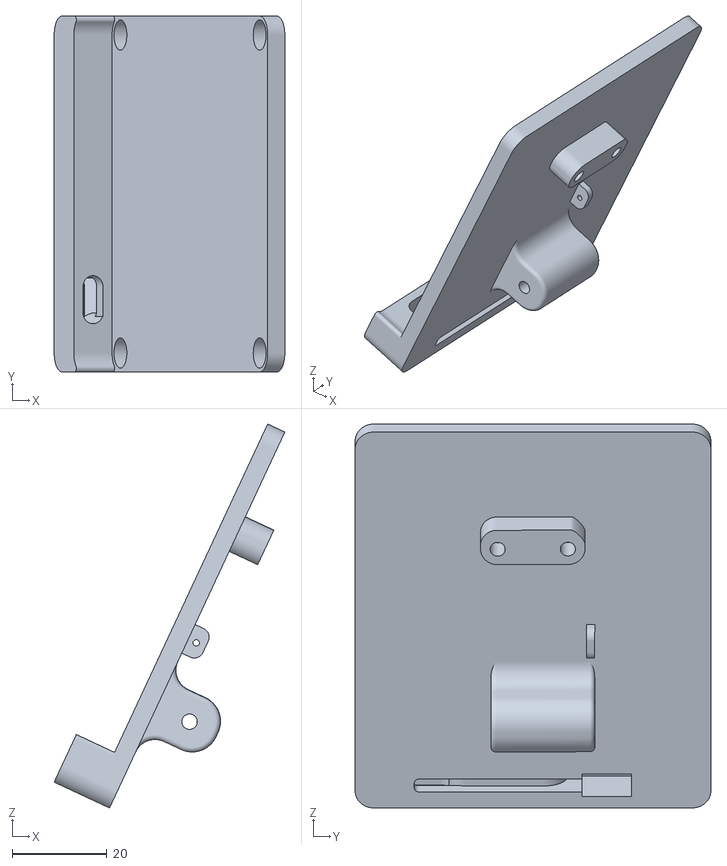
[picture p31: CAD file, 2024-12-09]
hardware/3dPrinted_Parts/PlayBot_Base.stl
48.6 x 75.0 x 80.9

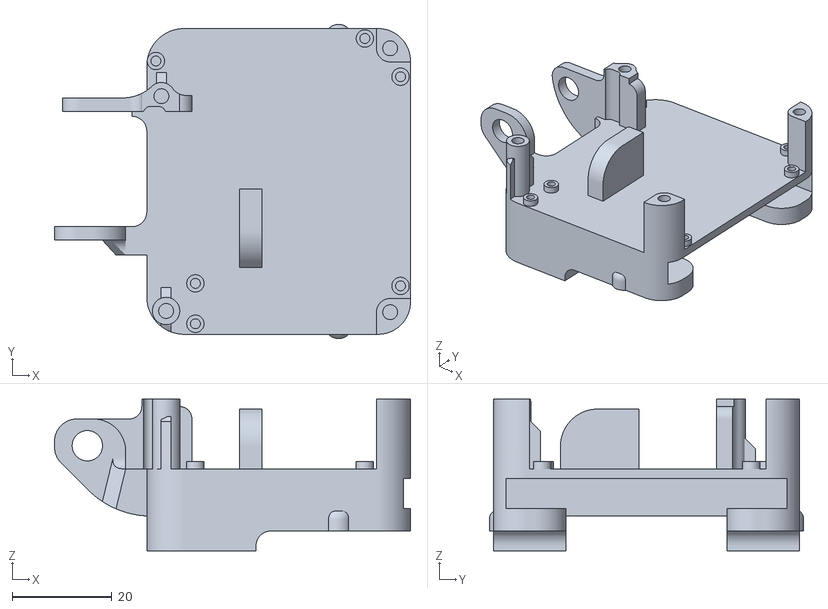
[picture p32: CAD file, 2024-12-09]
hardware/3dPrinted_Parts/PlayBot_UpperStage.stl
71.5 x 63.1 x 30.5

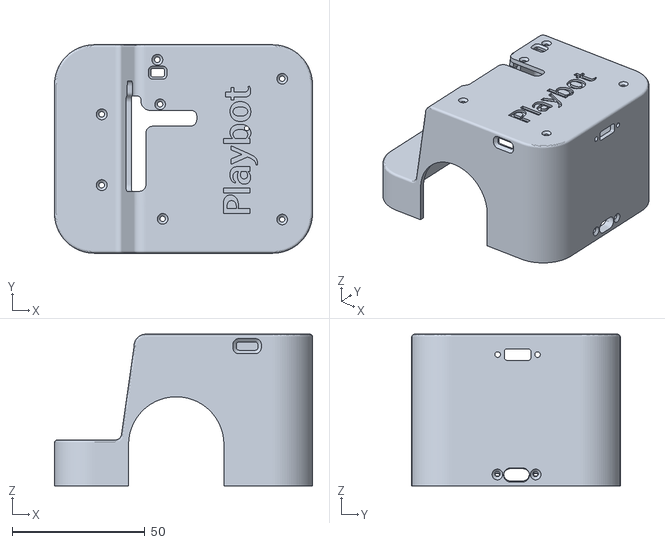
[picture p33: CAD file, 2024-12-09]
hardware/3dPrinted_Parts/PlayBot_Shell.stl
97.1 x 78.5 x 57.1

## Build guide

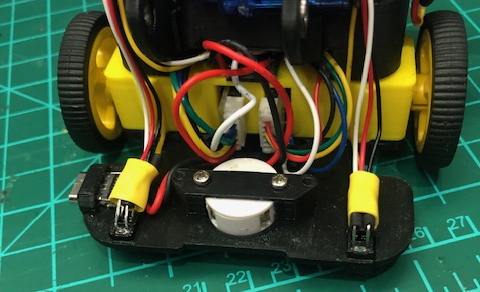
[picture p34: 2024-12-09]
images/Assembly_ITR.jpg

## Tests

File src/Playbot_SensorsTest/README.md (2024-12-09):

# PlayBot Sensor Test Program

A diagnostic tool for testing and calibrating PlayBot's hardware components.

## Hardware Requirements

- Teensy microcontroller
- DRV8835 motor driver
- 2x Quadrature encoders
- 2x IR sensors
- 2x ToF sensors with PCA9540BD multiplexer
- Light sensor
- MAX17048 battery gauge
- Servo motor for head movement

## Features

- Real-time sensor monitoring
- Motor movement testing
- Servo sweep testing
- Battery monitoring

## Commands

| Command | Description |
|---|---|
| `s` | Start continuous sensor monitoring |
| `t` | Test motors (forward/backward) |
| `v` | Test servo sweep movement |
| `c` | Center servo position |
| `h` | Display help message |

## Installation

1. Install required libraries:
   - Encoder
   - Adafruit_MAX1704X
   - PCA9540BD
   - DRV8835MotorShield
   - Servo

2. Upload to Teensy using Arduino IDE

## Usage

1. Open Serial Monitor (115200 baud)
2. Send 's' to start monitoring
3. Use commands to test specific components

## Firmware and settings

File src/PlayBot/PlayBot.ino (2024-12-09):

/**
 * Robot Controller - Main Program
 * 
 * This program controls a robot with various sensors and capabilities including:
 * - Motor control with encoders and PID
 * - Distance sensing (ToF sensors)
 * - Edge detection (IR sensors)
 * - Battery monitoring
 * - LED status indication
 * - Light sensing
 * - USB communication with host device
 * - SD card animation playback
 * - Servo control
 * 
 * Hardware requirements:
 * - Teensy board
 * - DRV8835 motor driver
 * - WS2812 LED
 * - ToF sensors with PCA9540BD multiplexer
 * - IR sensors
 * - MAX17048 battery gauge
 * - Servo motor
 * - SD card 
 */

// ================= Library Includes =================
#include "Config.h"
#include "HardwareConfig.h"
#include "Debug.h"
#include "StorageManager.h"
#include "DistanceTracker.h"
#include "LEDController.h"
#include "BatteryManager.h"
#include "AnimationManager.h"
#include "SensorManager.h"
#include "MotorController.h"
#include "CommunicationManager.h"
#include <string>
#include <PID_v1.h>
#include <SD.h>
#include <vector>
#include <Smoothed.h>

// ================= Global Objects =================
LEDController ledController(ws2812fx);
AnimationManager animationManager(headServo, motors, myEnc, myEnc2);
BatteryManager batteryManager(userial, ledController, animationManager);
DistanceTracker distanceTracker(myEnc, myEnc2);
String rightWheel, leftWheel;
SensorManager sensorManager(userial, animationManager, motors, ws2812fx, mux, 
                          myEnc, myEnc2, batteryManager, distanceTracker);
MotorController motorController(
    motors, 
    myEnc,      // Left encoder
    myEnc2,     // Right encoder
    myPID2,     // Left PID
    myPID,      // Right PID
    Setpoint,   // Right setpoint
    Setpoint2,  // Left setpoint
    Input,      // Right input
    Input2,     // Left input
    Output,     // Right output
    Output2     // Left output
);
StorageManager storageManager;
CommunicationManager communicationManager(
    myusb,
    userial,
    animationManager,
    batteryManager,
    sensorManager,
    motorController
);

// ================= Global Variables =================
bool MOTION_ENABLED = true;  // Initialize as enabled
unsigned long currentMillis = 0;

// ================= Main Setup Function =================
void setup() {
    // Initialize serial communication
    Serial.begin(9600);
    delay(1000);
    DEBUG_PRINT(DEBUG_INFO, "Setup started");
    //Initialize classes
    storageManager.initialize();
    sensorManager.initialize();
    ledController.initialize();
    motorController.initialize();
    batteryManager.initialize();
    communicationManager.initialize();
    distanceTracker.initialize();
    printSetupErrorSummary();

    DEBUG_PRINT(DEBUG_INFO, "Setup completed");

    // Set LED status based on setup success
    if (setupErrors.empty()) {
        ledController.setStatusSuccess();  // Green for success
    } else {
        ledController.setStatusError();    // Red for error
    }

    sendLogs();
}

// ================= Main Loop Function =================
void loop() {
    ledController.update();

    // Update system states
    motorController.updateTimers();
    motorController.updateEncoders();
    motorController.computePID();

    animationManager.getWheelCommands(rightWheel, leftWheel);
    motorController.updateSetpoints(rightWheel, leftWheel, animationManager.isAnimationPlaying());
    motorController.controlMotors(animationManager.isAnimationPlaying(), MOTION_ENABLED);

    // Handle animation if active
    animationManager.update();

    // Process USB communication and sensor checks
    communicationManager.readFromUSBHostSerialAndWriteToSerial();
    communicationManager.handleBaudRateChange();
    
    sensorManager.detectTableEdgeIR();
    sensorManager.checkLightSensor();
    sensorManager.checkFrontCollision();

    distanceTracker.update();
    distanceTracker.checkAndLog(animationManager.isAnimationPlaying());

    batteryManager.detectBatteryCharging();
    sendLogs();
    DEBUG_PRINT(DEBUG_VERBOSE, "Loop iteration completed");
}

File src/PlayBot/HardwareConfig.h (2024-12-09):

// HardwareConfig.h
#ifndef HARDWARE_CONFIG_H
#define HARDWARE_CONFIG_H

#include "PIDConfig.h"
// ================= Pin Assignments =================
// Motors
#define MOTOR1_PWM_PIN 7   // Left motor PWM
#define MOTOR1_DIR_PIN 6   // Left motor direction
#define MOTOR2_PWM_PIN 9   // Right motor PWM  
#define MOTOR2_DIR_PIN 8   // Right motor direction

// Encoders 
#define ENC1_PIN_A 4      // Left encoder A
#define ENC1_PIN_B 5      // Left encoder B
#define ENC2_PIN_A 3      // Right encoder A 
#define ENC2_PIN_B 2      // Right encoder B

// Sensors
#define IR_SENSOR_LEFT_PIN 39
#define IR_SENSOR_RIGHT_PIN 38
#define LIGHT_SENSOR_PIN 27
#define TOF_MULTIPLEXER_ADDR 0x70  // I2C address for ToF multiplexer

// Status & Control
#define LED_PIN 28
#define LED_COUNT 1
#define SERVO_PIN 23
#define SD_CS_PIN BUILTIN_SDCARD

// Battery Detection
#define USB_DETECT_PIN 17   
#define VOLTAGE_DIVIDER_RATIO (2.0/3.0)  // Voltage divider (2k/(1k+2k))

// ================= Hardware Constants =================
// Physical dimensions (mm)
#define WHEEL_DIAMETER 33.5f
#define WHEEL_BASE 81.0f     // Distance between wheels
#define ENCODER_PPR 813      // Pulses per revolution

#define MM_PER_TICK ((PI * WHEEL_DIAMETER) / ENCODER_PPR)
#define TICKS_PER_ROBOT_ROTATION (int)((PI * WHEEL_BASE * ENCODER_PPR) / WHEEL_DIAMETER)

// Motor characteristics
#define MOTOR_PWM_FREQUENCY 330000  // PWM frequency in Hz
#define MOTOR2_POWER_COMPENSATION 1.0f  // Compensation factor for motor 2
#define MOTOR1_POWER_COMPENSATION 1.0f  // Compensation factor for motor 1

// Include libraries 
#include <Encoder.h>
#include <DRV8835MotorShield.h>
#include <PID_v1.h>
#undef REVERSE  // Undefine REVERSE before PID
#include <WS2812FX.h>
#include <Servo.h>
#include <USBHost_t36.h>
#include "Adafruit_MAX1704X.h" 
#include <PCA9540BD.h>

// ================= Hardware Objects & Variables =================
// PID variables with inline initialization
inline double Input = 0, Output = 0, Setpoint = 0;
inline double Input2 = 0, Output2 = 0, Setpoint2 = 0;

// Core hardware objects
inline Encoder myEnc(ENC1_PIN_A, ENC1_PIN_B);
inline Encoder myEnc2(ENC2_PIN_A, ENC2_PIN_B);
inline DRV8835MotorShield motors(MOTOR1_PWM_PIN, MOTOR1_DIR_PIN, MOTOR2_PWM_PIN, MOTOR2_DIR_PIN);

// PID controllers
inline PID myPID(&Input, &Output, &Setpoint, PID_KP, PID_KI, PID_KD, AUTOMATIC);
inline PID myPID2(&Input2, &Output2, &Setpoint2, PID_KP, PID_KI, PID_KD, AUTOMATIC);

// Peripheral devices
inline WS2812FX ws2812fx(LED_COUNT, LED_PIN, NEO_GRB + NEO_KHZ800);
inline Servo headServo;
inline USBHost myusb;
inline USBHub hub1(myusb);
inline USBSerial_BigBuffer userial(myusb, 1);
inline PCA9540BD mux;
inline Adafruit_MAX17048 maxlipo;

#endif // HARDWARE_CONFIG_H

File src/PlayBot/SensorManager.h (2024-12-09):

// SensorManager.h
#ifndef SENSOR_MANAGER_H
#define SENSOR_MANAGER_H

#include "Config.h"
#include "Debug.h"
#include "BatteryManager.h"
#include "DistanceTracker.h"
#include <Wire.h>
#include <Smoothed.h>

// Manages all robot sensors and communicates with Playdate via messages:
// - "msg d/..." : Complete sensor data packet
// - "msg e/1" : Edge detected
// - "msg w/1" : Collision detected
// - "msg l/0|1" : Dark/Light state change
class SensorManager {
private:
    // ToF sensor variables with exponential smoothing 
    // to handle unreliable sensors
    Smoothed<float> TOFsensor1;        // Front sensor smoothing
    Smoothed<float> TOFsensor2;        // Back sensor smoothing
    float TOFsensorFront = 0;          // Cached front distance
    float TOFsensorBack = 0;           // Cached back distance
    unsigned char i2c_rx_buf[16];      // I2C reading buffer
    unsigned short lenth_val = 0;      // Current distance value

    // Light sensor state tracking
    unsigned long lastLightCheckTime = 0;
    bool isInDarkness = false;
    bool previousDarknessState = false;

    // Collision detection with enhanced validation
    unsigned long lastCollisionCheckTime = 0;
    bool collisionMessageSent = false;

    // IR edge detection with adjustable thresholds
    int IR_THRESHOLD_LEFT = 15;         // Left sensor threshold
    int IR_THRESHOLD_RIGHT = 15;        // Right sensor threshold
    unsigned long lastIRCheckTime = 0;
    bool isEdgeDetectedIR = false;
    Smoothed<float> smoothedIRLeft;     // IR value smoothing
    Smoothed<float> smoothedIRRight;    // IR value smoothing

    // Hardware interface references
    USBSerial_BigBuffer& userial;       // Serial communication
    AnimationManager& animationManager;  // Animation control
    DRV8835MotorShield& motors;         // Motor control
    WS2812FX& ws2812fx;                 // LED control
    PCA9540BD& mux;                     // ToF multiplexer
    Encoder& encoderLeft;               // Left wheel encoder
    Encoder& encoderRight;              // Right wheel encoder
    BatteryManager& batteryManager;     // Battery monitoring
    DistanceTracker& distanceTracker;   // Distance tracking

    // Read raw data from ToF sensor via I2C
    void SensorRead(unsigned char addr, unsigned char* datbuf, unsigned char cnt) {
        Wire.beginTransmission(82);
        Wire.write(byte(addr));
        Wire.endTransmission();
        Wire.requestFrom((uint8_t)82, (uint8_t)cnt);
        if (cnt <= Wire.available()) {
            *datbuf++ = Wire.read();
            *datbuf++ = Wire.read();
        }
    }

    // Convert raw ToF data to distance value
    int ReadDistance() {
        SensorRead(0x00, i2c_rx_buf, 2);
        lenth_val = i2c_rx_buf[0];
        lenth_val = lenth_val << 8;
        lenth_val |= i2c_rx_buf[1];
        return lenth_val;
    }

public:
    // Initialize manager with hardware references
    SensorManager(USBSerial_BigBuffer& serial, AnimationManager& anim, 
                 DRV8835MotorShield& mot, WS2812FX& led, PCA9540BD& multiplexer,
                 Encoder& encLeft, Encoder& encRight,
                 BatteryManager& battery, DistanceTracker& distance)
        : userial(serial)
        , animationManager(anim)
        , motors(mot)
        , ws2812fx(led)
        , mux(multiplexer)
        , encoderLeft(encLeft)
        , encoderRight(encRight)
        , batteryManager(battery)
        , distanceTracker(distance) {
        // Configure smoothing filters
        smoothedIRLeft.begin(SMOOTHED_EXPONENTIAL, 1000);
        smoothedIRRight.begin(SMOOTHED_EXPONENTIAL, 1000);
        TOFsensor1.begin(SMOOTHED_EXPONENTIAL, 2);    // Increased smoothing for unreliable ToF
        TOFsensor2.begin(SMOOTHED_EXPONENTIAL, 2);
    }

    // Initialize sensor hardware
    void initialize() {
        pinMode(IR_SENSOR_RIGHT_PIN, INPUT_DISABLE);
        pinMode(IR_SENSOR_LEFT_PIN, INPUT_DISABLE);
        DEBUG_PRINT(DEBUG_INFO, "IR sensors initialized");

        Wire.begin();
        DEBUG_PRINT(DEBUG_INFO, "ToF sensors initialized");
    }

    // Read distance from specific ToF sensor
    // Includes caching for reliability
    float readTofSensor(int channel) {
        mux.selectChannel(channel);
        float rawDistance = ReadDistance();
        
        if (rawDistance > 0) {
            if (channel == FRONT_SENSOR) {
                TOFsensorFront = rawDistance;
                return TOFsensorFront;
            } else {
                TOFsensorBack = rawDistance;
                return TOFsensorBack;
            }
        }
        
        return (channel == FRONT_SENSOR) ? TOFsensorFront : TOFsensorBack;
    }

    // Read averaged IR sensor values
    int readIRSensor(int sensorPin) {
        long sum = 0;
        const int numReadings = 10;
        
        for (int i = 0; i < numReadings; i++) {
            sum += analogRead(sensorPin);
        }
        return sum / numReadings;
    }

    // Monitor ambient light changes
    void checkLightSensor() {
        unsigned long currentTime = millis();
        if (currentTime - lastLightCheckTime >= LIGHT_CHECK_INTERVAL) {
            int lightValue = analogRead(LIGHT_SENSOR_PIN);
            bool currentDarknessState = (lightValue < DARKNESS_THRESHOLD);
            
            if (currentDarknessState != previousDarknessState) {
                isInDarkness = currentDarknessState;
                userial.println(isInDarkness ? "msg l/0" : "msg l/1");
                previousDarknessState = isInDarkness;
                DEBUG_PRINT(DEBUG_VERBOSE, "Light state changed. Is in darkness: " + String(isInDarkness));
            }
            
            lastLightCheckTime = currentTime;
            ws2812fx.setBrightness(isInDarkness ? 50 : 10);
        }
    }

    // Detect table edges using IR sensors
    void detectTableEdgeIR() {
        unsigned long currentTime = millis();
        if (currentTime - lastIRCheckTime >= IR_CHECK_INTERVAL) {
            float sensorLeftValue = readIRSensor(IR_SENSOR_LEFT_PIN);
            float sensorRightValue = readIRSensor(IR_SENSOR_RIGHT_PIN);
            
            bool currentEdgeDetected = (sensorLeftValue >= IR_THRESHOLD_LEFT || 
                                      sensorRightValue >= IR_THRESHOLD_RIGHT);
            
            if (currentEdgeDetected != isEdgeDetectedIR) {
                isEdgeDetectedIR = currentEdgeDetected;
                
                if (isEdgeDetectedIR) {
                    animationManager.stopAnimation();
                    motors.setM1Speed(0);
                    motors.setM2Speed(0);
                    userial.println("msg e/1");
                    DEBUG_PRINT(DEBUG_INFO, "Edge detected by IR sensors. Left: " + 
                              String(sensorLeftValue) + ", Right: " + String(sensorRightValue));
                }
            }
            
            lastIRCheckTime = currentTime;
        }
    }
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

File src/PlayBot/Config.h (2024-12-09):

// Config.h
#ifndef CONFIG_H
#define CONFIG_H

#include "PIDConfig.h"
#include "HardwareConfig.h"

// ================= Communication Settings =================
#define USBBAUD 115200
#define USB_BUFFER_SIZE 512

// ================= Light Sensor Configuration =================
#define LIGHT_CHECK_INTERVAL 200      // ms
#define DARKNESS_THRESHOLD 10

// ================= Edge Detection Configuration =================
#define EDGE_THRESHOLD 170            // mm
#define FRONT_SENSOR 1
#define BACK_SENSOR 0
#define EDGE_CHECK_INTERVAL 12        // ms

// ================= IR Sensor Configuration =================
#define IR_CHECK_INTERVAL 8           // ms

// ================= Battery Monitoring Configuration =================
#define BATTERY_CHECK_INTERVAL 250    // ms
// Battery thresholds
#define BATTERY_LOW_THRESHOLD 15.0f     // 15% battery threshold for warning
#define BATTERY_CRITICAL_THRESHOLD 5.0f  // 5% battery threshold for shutdown
// ================= Collision Detection Configuration =================
#define FRONT_COLLISION_THRESHOLD 70  // mm
#define COLLISION_CHECK_INTERVAL 4   // ms

// ================= Motion Constants =================

#define ROTATION_SPEED 200
extern bool MOTION_ENABLED;  // Global flag to control all motor movements
// ================= Distance Tracking =================
#define DISTANCE_UPDATE_INTERVAL 100   // ms
#define DISTANCE_LOG_INTERVAL 10000    // ms


#endif // CONFIG_H
